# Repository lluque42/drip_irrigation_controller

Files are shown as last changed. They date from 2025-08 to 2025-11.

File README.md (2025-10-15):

# Drip irrigation controller

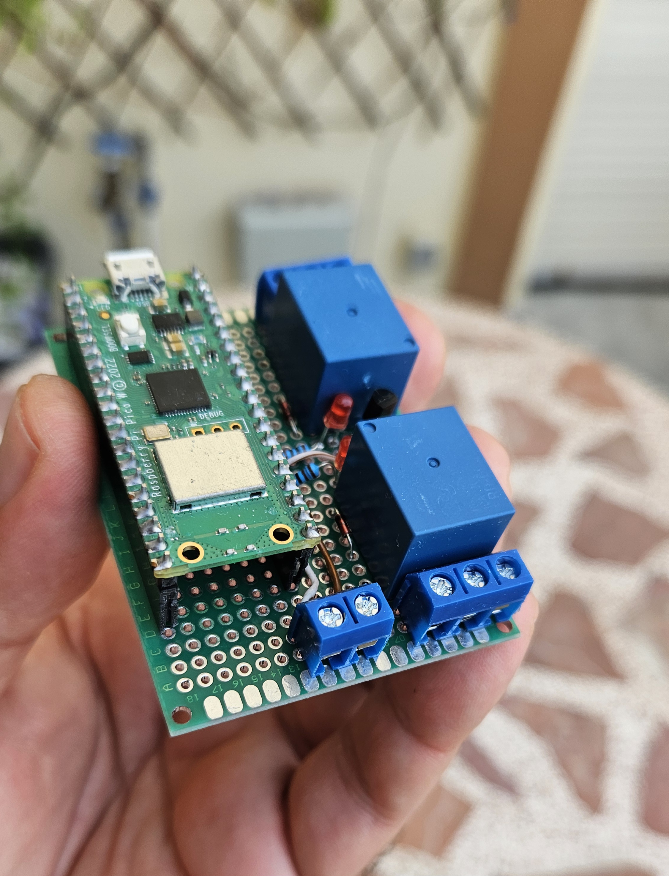
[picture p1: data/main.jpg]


## Table of contents

- [Introduction](#introductions)
- [Building instructions](#building-instructions)
- [WiFi connectivity](#wifi-connectivity)
    - [UDP command messages](#udp-command-messages)
- [Directory tree](#directory-tree)
- [Hardware](#harware)

------

## Introduction

This drip irrigation controller was designed to control one relay for a water
electrovalve and a second relay for ornament lights. Both relays may be
configured for independent one-time-a-day activation to remain active during a
configurable time. The frequency in terms of days between activations is also
configurable. Any of the relays may be disabled which will stop their future scheduled activations.

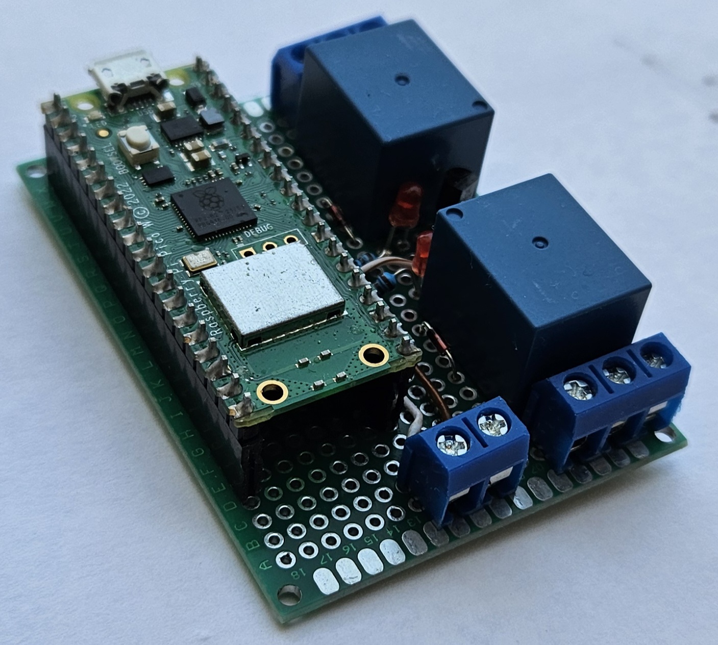
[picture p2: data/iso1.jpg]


A default configuration is applied at building time (edit files 'CMakeLists.txt',
'timers_default_data.cmake', and 'wlan_setup_data.cmake' to change it). The
controller configuration (get and set) and manual activation may be done
remotely through the wifi connection with simple UDP messages exchange.

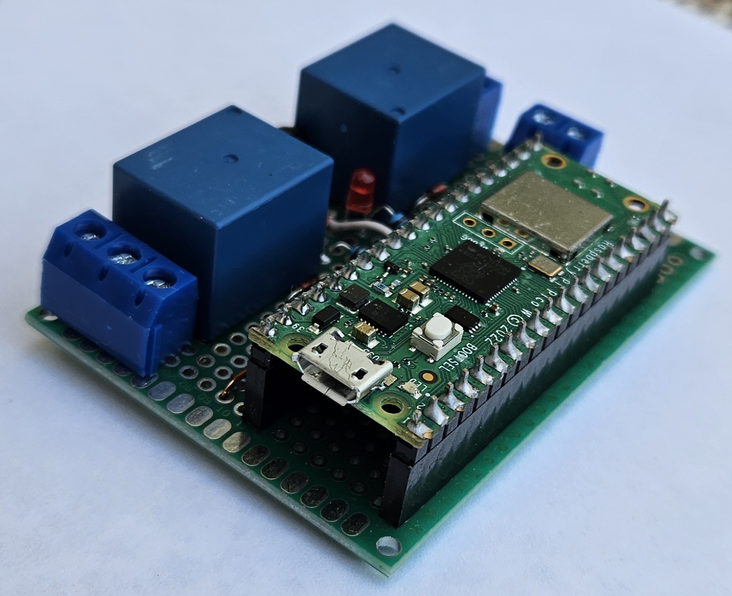
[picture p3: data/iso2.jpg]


This is the second controller I've built for my house plants.
The first was written in Python in a rush before going out on
a trip and worked perfectly. It had a dot matrix screen with
a setup menu through microswitches; a real-time clock module,
etc. But some years later it hangs a lot, outdoor installation
always takes its toll.

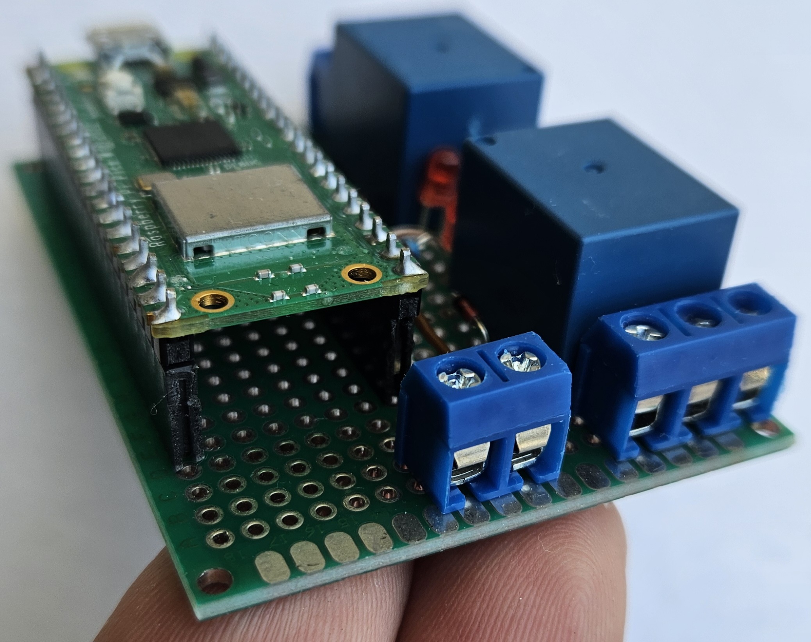
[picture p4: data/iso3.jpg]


So I've decided to implement a new version that loses the screen
in favor of a WiFi connection for keep-alive signaling against
a server, configuration and commands.

This repository includes all the code and scripts to built the
program in a Raspberry Pi Pico (1) W board. The schematics for
the external hardware is also included.

**Luis Luque - 2025**

------

## Building instructions

REMEMBER: This code was made for and tested on a Pico W (first
family of the Raspberry Pi Pico series). Use at your own risk in
other platforms.

Clone repository from:

https://github.com/lluque42/drip_irrigation_controller.git

Two files are included to allow an easy customization:
* wlan_setup_data.cmake.template (rename to wlan_setup_data.cmake)
    * To enter the wifi SSID, password.
* timers_default_data.cmake
* To enter the time of the day, frequency and duration for
the relays activation.

Create a build directory and enter to it:

```bash
drip_irrigation_controller $ mkdir build
drip_irrigation_controller $ cd build
drip_irrigation_controller/build $
```

Once inside, execute cmake against the parent directory (where
the CMakeLists.txt is):

```bash
drip_irrigation_controller/build $ cmake ..
drip_irrigation_controller/build $
```

If no errors occurred, then a Makefile file should have been created
in the build directory. Execute it to build the binaries.

```bash
drip_irrigation_controller/build $ make
```

If everything ok, a number of binary files should've been produced,
among them a drip.elf or drip.uf2 ready to be loaded into the Pico W
board.

For building the tests tool, see the **Wifi connectivity** section.

If some error occur check the pre-requisites:
* The PICO_SDK_VARIABLE environment variable should exist and point to
the root of the pico-sdk directory.
* Is your board really a Pico W (first generation)?
* ?
TODO

------

## WiFi connectivity

The microcontroller can connect to a wireless network if the correct settings
were edited in the wlan_setup_data.cmake file (a template for this file is
provided, just write your settings and rename the file).

A static IPv4 address must be provided, as well as an UDP port (a high
non-common one to avoid issues). This is necessary for the controller to act as
a simple text UDP server. That is, it will open the UDP port listening for
incoming messages. A set of message formats define commands and responses
that may be sent to the controller and back.

The messages are plain-text ASCII, human readable, strings (without the NUL
termination), that is, a string sent as the payload of the UDP datagram.

A simple, dirty client (and a server) written to debug this program is included
as a git sub-module in:

```bash
drip_irrigation_controller/test/udp_tx_rx
```

Since it is a submodule it should be initialized from the
drip_irrigation_controller root directory by doing:

```bash
drip_irrigation_controller $ git submodule update --init --recursive
```

After that, both the client and server can be build with:

```bash
drip_irrigation_controller/test/udp_tx_rx $ make
```

Which places the binaries in the bin folder.

To use the client to communicate over the wifi with  the irrigation controller
(assuming the default values in the wlan_setup_data.cmake.template) just do:

```bash
.../test/udp_tx_rx/bin $ ./udp_client 192.168.1.69 1234
```

This will receive input from the stdin for the user to send text to the
controller.

The commands, their formats, and the expected replies are the following:

------

### UDP command messages

Below are the recognized command messages and their replies. The client
just need to write and read this as the payload of UDP messages to/from
the controller that acts as a server on the IP address and UDP port set
in the wlan_setup_data.cmake at build time.
* Set datetime:
	SET:DATETIME:YYYY:MM:DD:dotw:HH:mm:SS
		dotw: Day of the week 0-6. Sunday is 0.
* Set water timer parameters:
    SET:WATER:WTODHH:WTODmm:WTODSS:WEXD:DOW
        TOD: Time of day when activation should occur.
        EXD: Every X days, the X. Days between activations.
        DO:  Duration of activation.
* Set lights timer parameters:
    SET:LIGHTS:LTODHH:LTODmm:LTODSS:LEXD:DOL
        TOD: Time of day when activation should occur.
        EXD: Every X days, the X. Days between activations.
        DO:  Duration of activation.
* Get datetime:
    GET:DATETIME
        Response example: 2025:8:15:5:21:2:52
        (see SET:DATETIME format).
* Get water relay current configuration:
    GET:WATER
        Response example: 
            21:0:0:1:120:2025:8:15:5:21:0:0
        That is:
            Time of day: 21:0:0
            Every X days: 1
            Duration (sec): 120
            Next activation scheduled: 2025:8:16:6:21:0:0
            (see SET:DATETIME format).
* Get lights relay current configuration:
    GET:LIGHTS 
        Response example:
            21:0:0:1:10800:2025:8:15:5:21:0:0
        See GET:WATER format.
* Manual on lights.
	MANUALON:LIGHTS
* Manual off lights.
	MANUALOFF:LIGHTS
* Manual on water.
	MANUALON:WATER
* Manual off water.
	MANUALOFF:WATER
* Timed on lights (Force turn on for the duration configured).
	TIMEDON:LIGHTS
* Timed on irigation (Force turn on for the duration configured).
	TIMEDON:WATER

For non get commands, expect a response of "done" if it was correctly processed
or a custom human readable error message.

------

## Directory tree

TODO

    ./  
    ├── .gitignore				(to prevent undesired files to be stagged)
    ├── Doxyfile				(doxygen config file for doc generation)  
    ├── Makefile				(use 'make help' for instructions)  
    ├── README.md				(brief documentation)  
    ├── doc/					(documentation extracted from comments in .h)  
    │   ├── html/				(html documentation)  
    │   │   ├── ...  
    │   │   ├── index.html		(entry point for html documentation)  
    │   │   ├── ...  
    │   └── man/				(man pages documentation)  
    │       └── man3/  
    │           └── ...			(example of use: 'man -l ft_string.h.3')  
    ├── include/				(directory for public header files (.h))  
    │   ├── ...  
    │   └── ...  
    ├── src/					(dir for source code and private header files)  
    │   ├── ...  
    │   │   ├── ...  				
    │   │   └── ...  
    │   └── ...					(may be structured in several directories)  
    │       ├── ...  
    │       └── ...  
    ├── lib/					(external libraries)  
    │   ├── ...  
    │   └── libft				(each library in its own directory)  
    ├── bin/					(directory for project's binaries and tester)  
    │   ├── ...  
    │   └── ...					(may be structured in several directories)  
    ├── obj/					(dir for source code and private header files)  
    │   ├── ...  
    │   │   ├── ...  
    │   │   └── ...  
    │   └── ...					(structured as in ./src)  
    │       ├── ...  
    │       └── ...  
    ├── data/					(directory for non-source files)  
    └── test/					(test program src code, compiles to .bin/tester)
        ├── ...  
        ├── tester.c  
        └── ...  

------

## Hardware

TODO

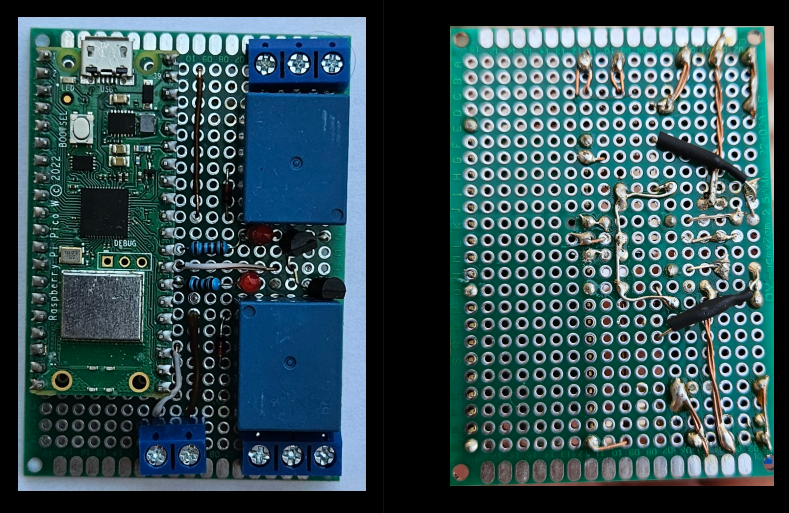
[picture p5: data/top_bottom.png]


Volts across led: 2,5 V 
	With a 10K resistance and driven through the 2n3904 (100KOhm base to gpio)

With USB 5V directly fed, the relay coil consumes 70mA
	The pico restarts everytime te coil de-energizes, the diode requirement is
	real.

Had to replace the 100K base resistor with a 10K because with the realy coil
current I guess the transistor couldn't remain polarized.

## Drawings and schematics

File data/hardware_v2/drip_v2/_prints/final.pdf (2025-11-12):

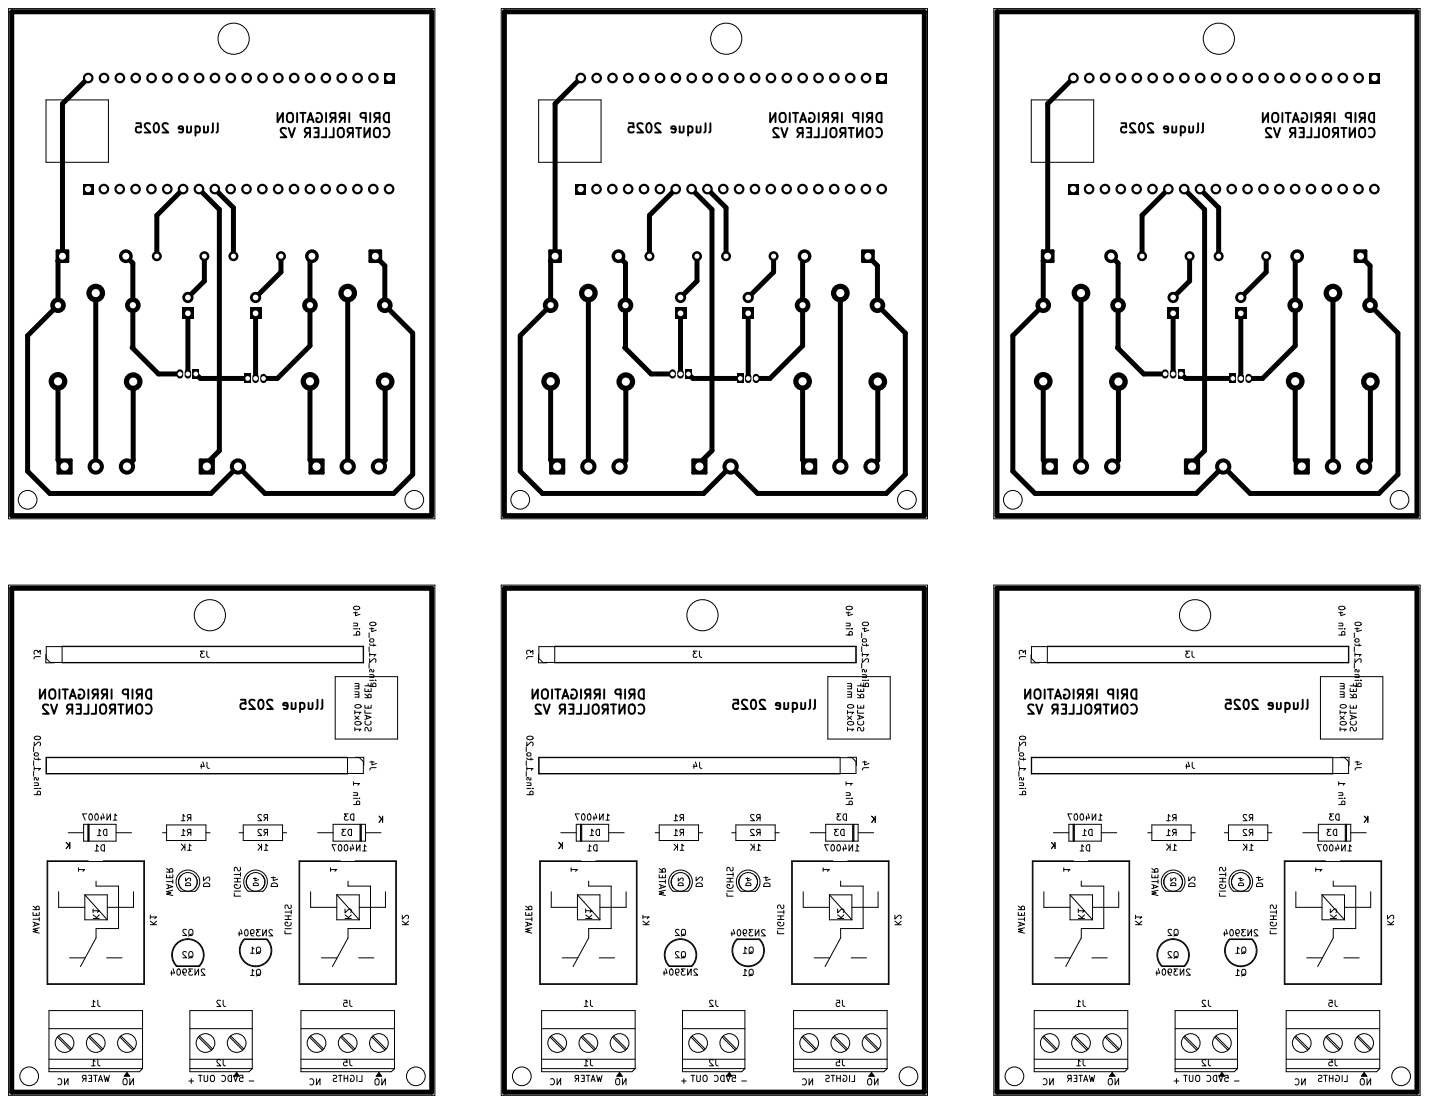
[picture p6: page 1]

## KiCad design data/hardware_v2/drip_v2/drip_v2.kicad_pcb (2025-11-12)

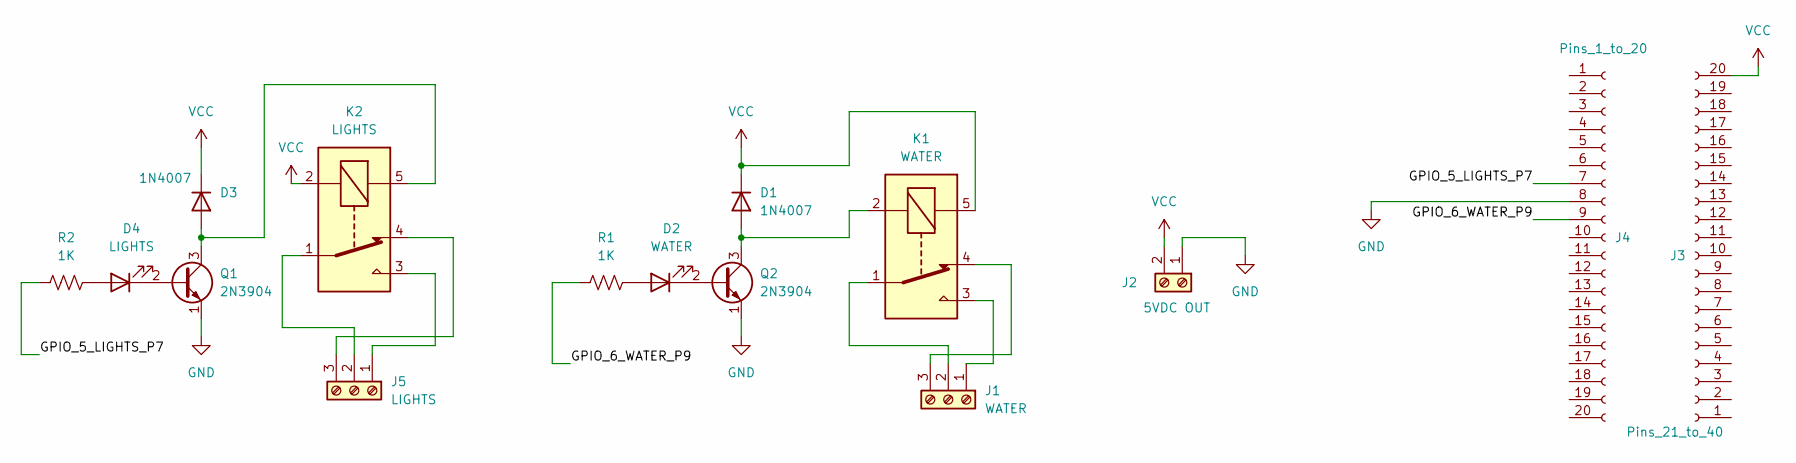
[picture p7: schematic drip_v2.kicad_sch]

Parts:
D1, D3: 1N4007; D_DO-41_SOD81_P10.16mm_Horizontal
D2: WATER; LED_D3.0mm
D4: LIGHTS; LED_D3.0mm
J1: WATER; TerminalBlock_Phoenix_MKDS-1,5-3_1x03_P5.00mm_Horizontal
J2: 5VDC OUT; TerminalBlock_Phoenix_MKDS-1,5-2_1x02_P5.00mm_Horizontal
J3: Pins_21_to_40; PinSocket_1x20_P2.54mm_Vertical
J4: Pins_1_to_20; PinSocket_1x20_P2.54mm_Vertical
J5: LIGHTS; TerminalBlock_Phoenix_MKDS-1,5-3_1x03_P5.00mm_Horizontal
K1: WATER; Relay_SPDT_SANYOU_SRD_Series_Form_C
K2: LIGHTS; Relay_SPDT_SANYOU_SRD_Series_Form_C
Q1, Q2: 2N3904; TO-92_Inline
R1, R2: 1K; R_Axial_DIN0207_L6.3mm_D2.5mm_P7.62mm_Horizontal

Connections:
/GPIO_5_LIGHTS_P7: J4.7, R2.1
/GPIO_6_WATER_P9: J4.9, R1.1
GND: J2.1, J4.8, Q1.1 (E), Q2.1 (E)
unnamed: D1.2 (A), K1.2, Q2.3 (C)
unnamed: D2.2 (A), R1.2
unnamed: D2.1 (K), Q2.2 (B)
unnamed: D3.2 (A), K2.5, Q1.3 (C)
unnamed: D4.2 (A), R2.2
unnamed: D4.1 (K), Q1.2 (B)
unnamed: J1.1, K1.3
unnamed: J1.2, K1.1
unnamed: J1.3, K1.4
unnamed: J5.1, K2.3
unnamed: J5.2, K2.1
unnamed: J5.3, K2.4
VCC: D1.1 (K), D3.1 (K), J2.2, J3.20, K1.5, K2.2

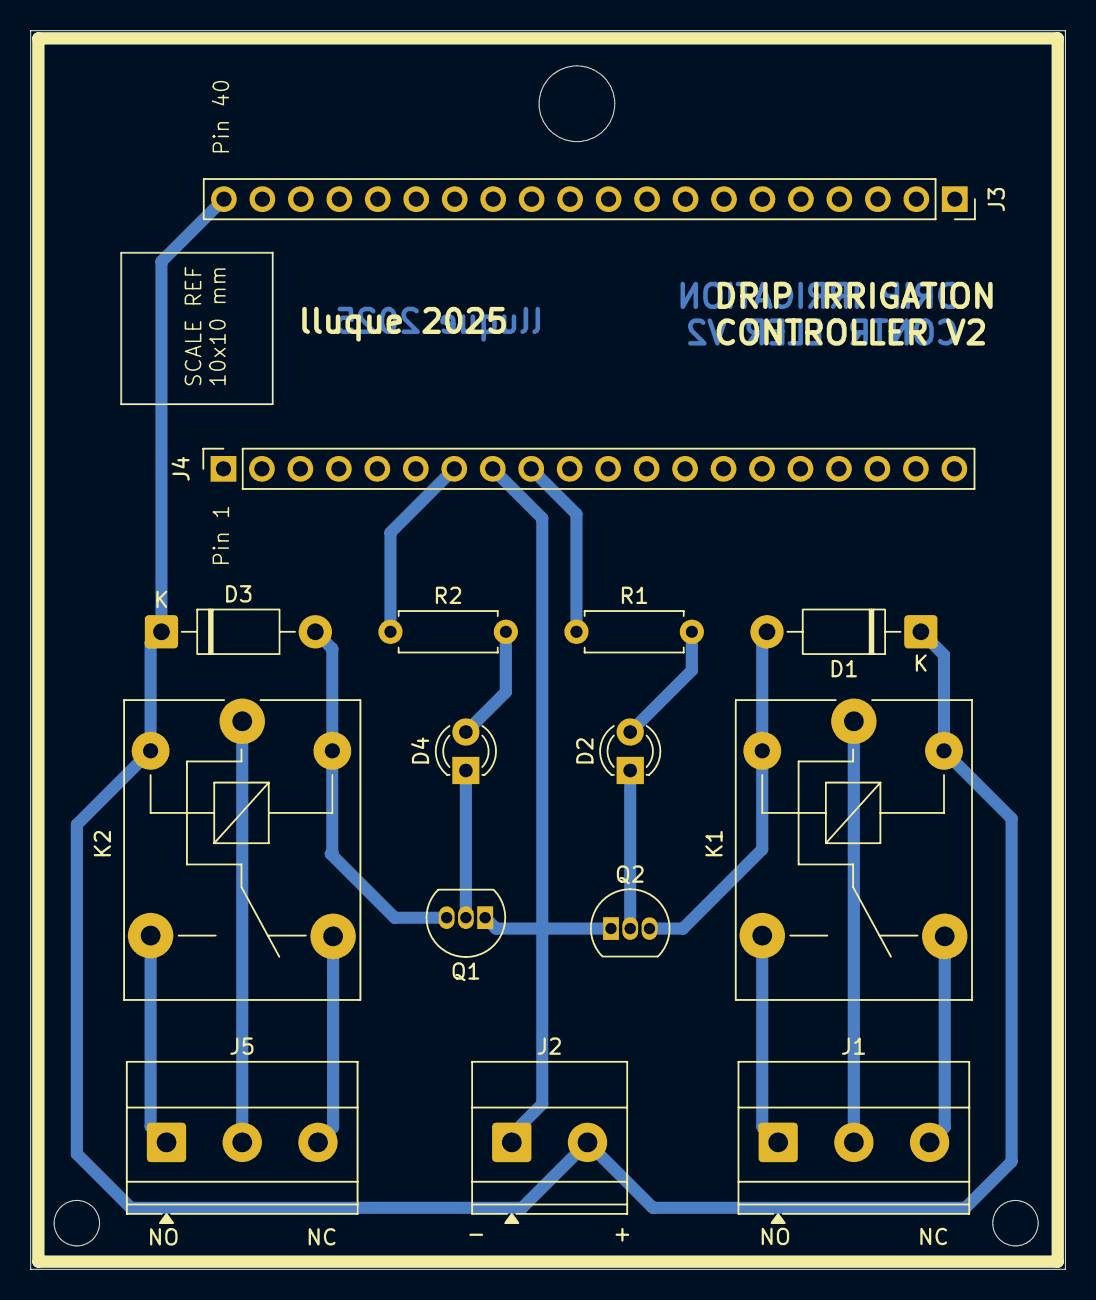
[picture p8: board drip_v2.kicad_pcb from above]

Board: 2 copper layers, 68.3 x 81.8 mm, 15 parts (0 on the bottom side), 16 nets.

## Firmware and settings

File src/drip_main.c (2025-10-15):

/* ************************************************************************** */
/*                                                                            */
/*                                                        :::      ::::::::   */
/*   drip_main.c                                        :+:      :+:    :+:   */
/*                                                    +:+ +:+         +:+     */
/*   By: lluque <lluque@student.42malaga.com>       +#+  +:+       +#+        */
/*                                                +#+#+#+#+#+   +#+           */
/*   Created: 2025/08/11 21:46:49 by lluque            #+#    #+#             */
/*   Updated: 2025/10/15 11:01:10 by lluque           ###   ########.fr       */
/*                                                                            */
/* ************************************************************************** */

#include "drip.h"

uint64_t		drip_time_offset_epoch_us = 0;

int main()
{
	t_drip_conf	*drip_settings;

	drip_bin_set_program_metadata();
	stdio_init_all();
	sleep_ms(1000);
	if (cyw43_arch_init())
		printf("Error initializing cyw43\n");
	drip_io_init();
	hard_assert(drip_time_rtc_init());
	drip_settings = drip_conf_load_settings_default();
	hard_assert(drip_settings != NULL);
	// This function enables wifi station mode (to connect to other APs),
	// sets the static IPv4 address and connects to the wifi.
	// If successful, it launches the udp server and other network services.
	if (!drip_wifi_init(drip_settings))
		printf("Error initializing wifi\n");
	while (1)
	{
		cyw43_arch_poll();
		// Polling must NOT be very frequent
		sleep_ms(5);
	}
	cyw43_arch_deinit();
}
//	 Something else to try if the CYW43 keeps hanging after approx. a day:
/*	printf("These are the settings:\nCYW43_DEFAULT_PM: '%0X'\nCYW43_NONE_PM: '%x'\n\
CYW43_AGGRESSIVE_PM: '%x'\nCYW43_PERFORMANCE_PM: '%x'\n",
		(unsigned int)CYW43_DEFAULT_PM,
		(unsigned int)CYW43_NONE_PM,
		(unsigned int)CYW43_AGGRESSIVE_PM,
		(unsigned int)CYW43_PERFORMANCE_PM);
*/
//	uint32_t	current_pm;
//	
//	cyw43_wifi_get_pm(&cyw43_state, &current_pm);
//	printf("The original power mode has '%0X'\n", (unsigned int)current_pm);
//		cyw43_pm_value(CYW43_DEFAULT_PM),
//		cyw43_pm_value(CYW43_NONE_PM),
//		cyw43_pm_value(CYW43_AGGRESSIVE_PM),
//		cyw43_pm_value(CYW43_PERFORMANCE_PM));
//	if (cyw43_wifi_pm(&cyw43_state, CYW43_NO_POWERSAVE_MODE))
//		printf("Error initializing setting power mode for cyw43\n");
//	cyw43_wifi_get_pm(&cyw43_state, &current_pm);
//	printf("The new power mode has '%0X'\n", (unsigned int)current_pm);
		// WARNING: polling very frequently will eventually make the
		// CYW43 stall (a tight poll loop with no sleep/delay).
		// Apparently (as in not officially documented): "if you poll too
		// aggressively in a tight loop with no yield (busy loop),
		// the FreeRTOS/lwIP timeouts don’t advance properly, and eventually
		// DHCP, ARP cache, or internal timers can stall."
		// "The lwIP stack requires periodic timer servicing. Normally
		// sys_check_timeouts() is called from the polling loop. The Pico SDK
		// cyw43_arch_poll() will call it for you only if enough time has
		// elapsed. But if you never sleep, the "elapsed time" logic might
		// not trigger properly."
		// "Since you’re running a UDP server, ARP table expiry can break
		// communication after some hours if ARP requests are not serviced
		// properly. That again ties back to lwIP timers needing to run
		// consistently. If ARP table cleanup doesn’t happen, packets won’t get
		// delivered."
		//
		// Solutions:
		// 		* Adding sleep_ms(1);
		// 		* Adding tight_loop_contents(); which "expands to __wfe() (the
		// 		ARM “Wait For Event” instruction), which tells the CPU to idle
		// 		until an event happens, reducing power consumption and freeing
		// 		up cycles."
		// 		* Adding cyw43_arch_wait_for_work_until(some_time);
		// 			"Best for production UDP/TCP servers — integrates with lwIP
		// 			timers and Wi-Fi events properly, avoids wasting CPU cycles.
		// 			This is the most robust long-term choice for a polling UDP
		// 			server that should run for days/weeks."
		//
		// Didn't prevent the cyw43 with 5 ms
		//cyw43_arch_wait_for_work_until(make_timeout_time_ms(DRIP_WAIT_WIFI_MS));
		// Didn't prevent it. Tested along with the periodic
// This didn't prevent the wifi hang, it actually kept saying CYW43_LINK_JOIN
//int64_t	drip_wifi_check_health(alarm_id_t id, void *arg)
//{
//	t_drip_conf	*settings;
//	int			status;
//	datetime_t  t;
//	char		buffer[DRIP_WIFI_STATE_MSG_BUFSIZE];
//	
//	memset(buffer, 0, DRIP_WIFI_STATE_MSG_BUFSIZE);
//	id = id;				// Just to avoid the strict warnings
//	settings = (t_drip_conf *)arg;
//	settings = settings;	// Just to avoid the strict warnings
//	if (!rtc_get_datetime(&t))
//		return (DRIP_WIFI_CHECK_MS * 1000);					// TODO error check..................
//	datetime_to_str(buffer, DRIP_WIFI_STATE_MSG_BUFSIZE, &t);
//	buffer[strlen(buffer)] = ':';
//	status = cyw43_wifi_link_status(&cyw43_state, CYW43_ITF_STA);
//	if (status == CYW43_LINK_DOWN)
//		memmove(buffer + strlen(buffer),
//				"CYW43_LINK_DOWN",
//				DRIP_WIFI_STATE_MSG_BUFSIZE - strlen(buffer));
//	if (status == CYW43_LINK_JOIN)
//		memmove(buffer + strlen(buffer),
//				"CYW43_LINK_JOIN",
//				DRIP_WIFI_STATE_MSG_BUFSIZE - strlen(buffer));
//	if (status == CYW43_LINK_FAIL)
//		memmove(buffer + strlen(buffer),
//				"CYW43_LINK_FAIL",
//				DRIP_WIFI_STATE_MSG_BUFSIZE - strlen(buffer));
//	if (status == CYW43_LINK_NONET)
//		memmove(buffer + strlen(buffer),
//				"CYW43_LINK_NONET",
//				DRIP_WIFI_STATE_MSG_BUFSIZE - strlen(buffer));
//	if (status == CYW43_LINK_BADAUTH)
//		memmove(buffer + strlen(buffer),
//				"CYW43_LINK_BADAUTH",
//				DRIP_WIFI_STATE_MSG_BUFSIZE - strlen(buffer));
//	puts(buffer);
//	return (DRIP_WIFI_CHECK_MS * 1000);
//}




//	// While debugging (or if the board was visible in this application,
//	// this comes handy as a heartbeat. Call from the main loop.
//		drip_toggle_on_board_led(&on_board_led_status);
//
//	// NOTE: I couldn't make it work as a callback with a timer may be because
//	// being a CWY43 GPIO it conflicts when manipulated from an IRQ
//	static void	drip_toggle_on_board_led(bool *on_board_led_status)
//	{
//		//	// It requrires this outside:
//		//	#define DRIP_TOGGLE_ON_BOARD_LED_MS 500
//		//
//		//	// It requrires this outside the loop:
//		//	//	bool			on_board_led_status;
//	
//		//	// After cyw43_arch_init()
//		//	cyw43_arch_gpio_put(ON_BOARD_LED, 1);
//		//	*on_board_led_status = true;
//		if (*on_board_led_status)
//		{
//			cyw43_arch_gpio_put(ON_BOARD_LED, 0);
//			*on_board_led_status = false;
//		}
//		else
//		{
//			cyw43_arch_gpio_put(ON_BOARD_LED, 1);
//			*on_board_led_status = true;
//		}
//		sleep_ms(DRIP_TOGGLE_ON_BOARD_LED_MS);
//	}
//	// To avoid IRQ-unsafe operations, just set a global flag in a callback
//	// but service it outside in the main loop.
//	// This global
//	int				print_settings_pending = 0;
//
//	// This inside the main loop:
//	if (print_settings_pending)
//	{
//		print_settings_pending = 0;
//		printf("[main] A print_settings_pending\n");
//		drip_conf_print_settings(drip_settings);
//	}
//
//
//	// Another useful heartbeat when having RTC applications is this 
//	// repeating low-level alarm.
//	// In main()
//	datetime_t	alarm_pattern;
//	
//	// Values of -1 indicate don't care, i.e. no need to match.
//	hard_assert (drip_rtc_str2datetime(	"-1:-1:-1:-1:-1:-1:0",
//											&alarm_pattern, 1));
//	//rtc_set_alarm(&alarm_pattern, timer_alarm);
//	
//	The callback:
//	void	timer_alarm(void)
//	{
//		datetime_t	t;
//		char		time_str[200];
//	
//		printf("[timer_alarm] Alarm works\n");
//		if (!rtc_get_datetime(&t))
//			printf("[timer_alarm] RTC not working\n");
//		else
//		{
//			datetime_to_str(time_str, sizeof(time_str), &t);
//			printf("%s\n", time_str);
//		}
//	}

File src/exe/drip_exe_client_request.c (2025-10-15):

/* ************************************************************************** */
/*                                                                            */
/*                                                        :::      ::::::::   */
/*   drip_exe_client_request.c                          :+:      :+:    :+:   */
/*                                                    +:+ +:+         +:+     */
/*   By: lluque <lluque@student.42malaga.com>       +#+  +:+       +#+        */
/*                                                +#+#+#+#+#+   +#+           */
/*   Created: 2025/08/13 22:55:23 by lluque            #+#    #+#             */
/*   Updated: 2025/08/28 16:07:53 by lluque           ###   ########.fr       */
/*                                                                            */
/* ************************************************************************** */

#include "drip.h"

struct pbuf	*drip_exe_build_pbuf_from_str(char *str)
{
	struct pbuf	*p;
	
	p = pbuf_alloc(	PBUF_TRANSPORT,
					strlen(str),
					PBUF_RAM);
	// if (== NULL...
	memcpy(p->payload, (void *)str, p->len);
	return (p);
}

/*
 * See README.md for details on the command message formats.
*/
struct pbuf	*drip_exe_client_request(struct pbuf *p, t_drip_conf *drip_settings)
{
	char	*token;
	char	*saveptr;	// For re-entrant strtok
	char	*request;


	// TODO chained pbuf??????? if so, error



	// Changed to a string for easier parsing
	request = calloc(p->len + 1, sizeof(char));
	//if (== NULL)...
	memcpy((void *)request, p->payload, p->len);
	// request comes from the pbuf: (char *)p->payload
	// It is free in the caller after this returns so...
	// I believe there's no issue with editing it.
	// NOT ANYMORE... now request is a temporary string
	// that MUST BE FREED HERE!
	//printf("p->len = '%d'\n", p->len);
	//printf("stringified payload: '%s'\n", request);
	token = strtok_r(request, ":", &saveptr);
	if (NULL)
		return (free(request), drip_exe_build_pbuf_from_str("Malformed request"));
	if (strcmp("SET", token) == 0)
	{
		token = strtok_r(NULL, ":", &saveptr);
		if (strcmp("DATETIME", token) == 0)
		{
			datetime_t	time;
			
			// The time_str actually begins after the \0 of DATETIME
			// so some manipulation must be done
			token = strtok_r(NULL, ":", &saveptr);
			// Now token is YYYY\0, then we change back the delimiter
			token[strlen(token)] = ':';
			if (!drip_time_str2datetime(token, &time, 0))
				return (free(request), drip_exe_build_pbuf_from_str("Couldn't set time, err1"));
			if (!rtc_set_datetime(&time))
				return (free(request), drip_exe_build_pbuf_from_str("Couldn't set time, err2"));
			//printf("[drip_exe_client_request] time set, re-scheduling activations...\n");
			//printf("[drip_exe_client_request] This is the current configuration...\n");
			//drip_conf_print_settings(drip_settings);
			if (!drip_conf_enforce_settings(drip_settings))
				return (free(request), drip_exe_build_pbuf_from_str("Time set but couldn't re-schedule timers!"));
			return (free(request), drip_exe_build_pbuf_from_str("done"));
		}
		else if (strcmp("WATER", token) == 0)
		{
			//SET:WATER:WTODHH:WTODmm:WTODSS:WEXD:DOW
			//	SET:WATER:18:50:23:2:120
			token = strtok_r(NULL, ":", &saveptr);
			if (token == NULL)
				return (free(request), drip_exe_build_pbuf_from_str("Malformed request, missing hour"));
			else
			{
				errno = 0;
				drip_settings->wtod_alarm.hour = (int)strtol(token, NULL, 10);
				if (errno != 0 || drip_settings->wtod_alarm.hour > 23
					|| drip_settings->wtod_alarm.hour < 0)
					return (free(request), drip_exe_build_pbuf_from_str("Malformed request, invalid value for hour"));
			}
			token = strtok_r(NULL, ":", &saveptr);
			if (token == NULL)
				return (free(request), drip_exe_build_pbuf_from_str("Malformed request, missing minute"));
			else
			{
				errno = 0;
				drip_settings->wtod_alarm.min = (int)strtol(token, NULL, 10);
				if (errno != 0 || drip_settings->wtod_alarm.min > 59
					|| drip_settings->wtod_alarm.min < 0)
					return (free(request), drip_exe_build_pbuf_from_str("Malformed request, invalid value for minute"));
			}
			token = strtok_r(NULL, ":", &saveptr);
			if (token == NULL)
				return (free(request), drip_exe_build_pbuf_from_str("Malformed request, missing second"));
			else
			{
				errno = 0;
				drip_settings->wtod_alarm.sec = (int)strtol(token, NULL, 10);
				if (errno != 0 || drip_settings->wtod_alarm.sec > 59
					|| drip_settings->wtod_alarm.sec < 0)
					return (free(request), drip_exe_build_pbuf_from_str("Malformed request, invalid value for sec"));
			}
			token = strtok_r(NULL, ":", &saveptr);
			if (token == NULL)
				return (free(request), drip_exe_build_pbuf_from_str("Malformed request, missing days between water"));
			else
			{
				errno = 0;
				drip_settings->wexd = (int)strtol(token, NULL, 10);
				if (errno != 0 || drip_settings->wexd > DRIP_MAX_WEXD
					|| drip_settings->wexd < DRIP_MIN_WEXD)
					return (free(request), drip_exe_build_pbuf_from_str("Malformed request, invalid value for days between water"));
			}
			token = strtok_r(NULL, ":", &saveptr);
			if (token == NULL)
				return (free(request), drip_exe_build_pbuf_from_str("Malformed request, missing duration of water"));
			else
			{
				errno = 0;
				drip_settings->dow_sec = (int)strtol(token, NULL, 10);
				if (errno != 0 || drip_settings->dow_sec > DRIP_MAX_DOW
					|| drip_settings->dow_sec < DRIP_MIN_DOW)
					return (free(request), drip_exe_build_pbuf_from_str("Malformed request, invalid value for days between water"));
			}
			//printf("[drip_exe_client_request] time set, re-scheduling activations...\n");
			//printf("[drip_exe_client_request] This is the current configuration...\n");
			//drip_conf_print_settings(drip_settings);
			if (!drip_conf_enforce_settings(drip_settings))
				return (free(request), drip_exe_build_pbuf_from_str("Time set but couldn't re-schedule timers!"));
			return (free(request), drip_exe_build_pbuf_from_str("done"));
		}
		else if (strcmp("LIGHTS", token) == 0)
		{
			//SET:LIGHTS:LTODHH:LTODmm:LTODSS:LEXD:DOL
			//	SET:DATETIME:2025:8:15:5:19:07:0
			//	SET:LIGHTS:19:07:23:2:12
			//	SET:WATER:19:07:33:1:12
			token = strtok_r(NULL, ":", &saveptr);
			if (token == NULL)
				return (free(request), drip_exe_build_pbuf_from_str("Malformed request, missing hour"));
			else
			{
				errno = 0;
				drip_settings->ltod_alarm.hour = (int)strtol(token, NULL, 10);
				if (errno != 0 || drip_settings->ltod_alarm.hour > 23
					|| drip_settings->ltod_alarm.hour < 0)
					return (free(request), drip_exe_build_pbuf_from_str("Malformed request, invalid value for hour"));
			}
			token = strtok_r(NULL, ":", &saveptr);
			if (token == NULL)
				return (free(request), drip_exe_build_pbuf_from_str("Malformed request, missing minute"));
			else
			{
				errno = 0;
				drip_settings->ltod_alarm.min = (int)strtol(token, NULL, 10);
				if (errno != 0 || drip_settings->ltod_alarm.min > 59
					|| drip_settings->ltod_alarm.min < 0)
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

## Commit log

2025-08-07 ADD gitignore and basic building capabilities
    A heavily commented template for CMakeLists.txt was added from
    scratch to test and document my knowledge. The "pico_sdk_import.cmake"
    was copied from the SDK directory. A dummy main.c was added. It
    builds with no problem.
    In the CMakeLists.txt I tried a couple of strategies to build
    with no additional arguments (board type, wlan connection data) and
    seemed to work fine.
2025-08-09 ADD RTC and alarm capabilities, on-board LED
    The setting and getting of date time using the RP-2040 internal RTC
    was tested succesfully. Also the alarm feature in terms of absolute
    time (when a particular value of any of the non-minus-one time fields
    match with the current time) was tested using a callback function of
    mine.
    The on-board LED control was also tested. The board is a Pico W so
    the on-board LED doesn't connect to a RP-2040 gpio but to a gpio
    on the wifi chip (the CYW43), requiring a different setup.
2025-08-11 ADDed WiFi capabilities and static ip address
    More proof-of-concepts achieved regarding the network capabilities.
    I had to deep into the lwIP own documentation and source code to
    understand a couple of things and get the desired results.
    The generic lwipopts.h was added.
    Also a document for some comments on the hardware.
    By the way, in the real world and against all odds, I manage to
    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
2025-08-11 REFACTORIZATION The first serious clean up
    A more organized tree directory was built. Functions were taken
    out the main.c, renamed with a prefix to show their functionality
    area, and put into their own files.
    A template for the WiFi configuration was added with useful comments
    for a straight forward customization: wlan_setup_data.cmake.template.
    In a similar fashion, another file was added with the default timers
    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
2025-08-13 ADDed more network capabilities: UDP server
    The UDP server that receives and echoes bytes is working.
    When a NUL terminated c-string "1" is received, the water relay
    coil is energized, with "3" it's turned off. The same for the
    lights relay with "2" (ON) and "4" (OFF).
    The authentication type was added to the
    wlan_setup_data.cmake.template using the macros defined by cyw43:
    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
2025-08-14 ADDed loading of default settings from build data
    Improved drip_rtc_str2datetime() with more fool-proof error checking.
    Added a struct type for the timers setting values and a function to
    load them from the buildtime macro values on timers_default_data.cmake.
    The default settings from CMake macros are now loaded into the program.
2025-08-15 ADD Scheduled relay activaton for required durations
    Activation and de-activation of relays by chaining alarm scheduling
    was added. The API used was the pico_time alarm pool that uses
    absolute time (usec since boot) so utils functions for time
    conversion amd manipulation were added (e.g. human-readable
    datetime_t struct to usec epoch; uint64 usec relative time offset
    of the absolute time to the usec epoc RTC at the time of setting)
    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
2025-08-16 ADDed remote control & config WiFi-UDP
    Implemented the "every 0 days" option meaning do-not-schedule.
    Added more strict compilation flags and fixed every pending warning.
    A description and the repo url were added as binary metadata.
    Added a generic mechanism (beyond loading and applying the default
    settings) to allow the enforcement of new settings during runtime:
    cancel scheduled alarms, re-compute the RTC time offset,
    calculate new alarms, etc.
    Implemented the remote commands as plain-text ascii nul terminated
    C-strings as payloads of an UDP datagram. The README.md file was
    updated with the details. The commands can be tried using the simple
    UDP client added a few commits ago.
    A summa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
    [drip_exe_client_request.c]
2025-10-15 FIX wifi unresponsive after a day
    The lwiopts.h was modified to disable the DHCP. The static
    address is configured before connecting to the WLAN. This
    proved to be the solution for the freezing of the wifi
    connection after some time working fine.
    Some refactorization was made.
    [drip_exe_client_request.c]
2025-11-12 New hardware
    A new PCB was designed to replace the old one that got wet.
    The outputs were moved to new GPIOs.
    [drip_v2.kicad_pcb, drip_v2.kicad_sch]
